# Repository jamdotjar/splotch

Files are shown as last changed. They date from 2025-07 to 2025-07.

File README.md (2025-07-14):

Card_Outline(3)
# SPLOTCH:
(**S**CARA **PLOT**ter that's **CH**eap).

SPLOTCH is a parallel arm SCARA plotter, that can *usually* trick people into
thinking it draws what it's meaning to.

This project was built in 72 hours as part of the Undercity Hackathon in SF, and
it's state does represent that.



https://youtu.be/LqYqyEfOcu8

# Development
Going into this, I had literally no idea how to make a robot arm, and here I am
now, with still almost no idea how to make a robot arm.  Anyways, we made this.
We started by researching different mechanisms, we settled on this because it
didn't need a belt, and kept the arms relatively light. Servos were used for
their relative ease of use over steppers, and the fact they didn't need
dedicated driver boards which were in very short supply.  The first versions of
the arm assembly were designed to not require screws, but the relative
unreliability of PLA lead to a lot of broken parts, and thus the decisiion to
screw literally everything together. ( exept for the pen holder, which was most
efficient to do snap fit )

# Make your own!
Considering the relatively lightweight requirements, you can build your own SCARA plotter with a few servos, some 3d printed parts, and a pen. Specifically, you will need:
| Component | Description | Quantity | Link |
|---|---|---|---|
| Servos | G996R or similar for arm joints, and pen lifter | 3 | https://towerpro.com.tw/product/sg90-analog/ |
| 3D printed parts | 4 3D printed arms, servo holder, and case | 1 | |
| Rotary encoders | For manual control (etch-a-sketch mode!), we used EC11's | 2 | |
| Pen | Any standard pen or marker, should be no more than 9mm in diameter near the head. | 1 | | 
| Microcontroller | Raspberry Pi pico | 1 | https://www.raspberrypi.com/products/raspberry-pi-pico/ |
| Wiring | Dupont Jumper wires| ~ |  |
| Sticky tape or glue | For securing the servos, double sided tape is pretty good | ~ | |
| Breadboard | wiring aid | 1| |
| M.2 screws longer than 5mm | for attaching arms together | 4 |
| Baseplate | A flat-ish base to mount everything on, we used cardboard| 1 | |

### Assembly
1. Print all 3D parts, or get some elsewhere.
2. put the servos in the holder, and fix them in place with double sided tape or
   glue.
3. Attach the holder to the baseplate, in the center of the bottom edge. The
   curved corners of the baseplate should be facing forwards, and the wires of
   the servos should be facing backwards.
4. Attach the front and back links of each arm. The m.2 screw should pass
   through the first arm and bore into the second arm, securing them together
   and allowing room for rotation. The screws on the two front arms will face
   opposite directions, and the screws on the two back arms will face opposite
   directions.
   The front arm should be on the top, and the back arm should be on the bottom.

   

6. Attach the third servo to the end of the arm, in the small slot.
7. Wire up the motors, and rotary encoders, referencing this wiring diagram:


8. attach the breadboard and servo holder to the baseplate
9. Place the case over the breadboard, make sure to reconnect wires properly
10. Insert rotary encoders into the slots on the lid (maybe use glue), slide in
   the lid.
11. Done!

# Usage
1. Connect the Raspberry Pi Pico to your computer via USB.
2. Setup python enviroment by running:
```bash
pip install -r requirements.txt
```
3. Flash the firmware to the Pico by running:
```bash
mpremote connect auto fs cp firmware/main.py :
```
4. use minicom or any other serial terminal to connect to the Pico:
```bash
minicom -D /dev/tty.usbmodem1101 -b 115200
```
5. Once connected, you can send commands to the plotter, you can use the
   following commands:
   - `angle_a,angle_b` - Move to servo angles (e.g. `120,60`)
   - `xy:x,y` - Move to XY coordinates (e.g. `xy:50,80`)
   - `pen:up`, `pen:down` or `pen:dot` - Move pen up or down, or do both
     (down-up)
   - `safe:x,y,w,h` - Set safe zone (paper) parameters (e.g.
     `safe:-50,100,100,100`)
   - `safe:on` or `safe:off` - Enable or disable safe zone checks
   - `enc:on` or `enc:off` - Enable or disable encoder (manual) control")
   - `enc:step:N` - Set encoder sensitivity (N = degrees per step, e.g.
     `enc:step:0.5`
   - `exit` - Quit program
  Command can be chained together with a semicolon, e.g.
  `angle_a,angle_b;xy:x,y;pen:up`
6. To generate complex strings of commands, you can either use visualizeIK.py to
   draw your own, or use the SVG to commands script to convert an SVG file into
   a set of commands.
7. - Use ik_path_planner.py to draw your own commands:
   - Run `python3 firmware/ik_path_planner.py`
   - Click on the canvas to add a point, adding subsequent points will create a
     line between them. To raise the head, click the "Pen Up" button, and to
     lower it, click the "Pen Down" button. to create a dot at your current
     position, click the "Pen Dot" button.
   - Once you are done, click the "Generate Commands" button to generate a set
     of commands based on the points you have drawn.
   - The generated commands will be printed to the console.
   - Copy the commands to your clipboard and paste them into the serial terminal
     to see them executed.



# Images




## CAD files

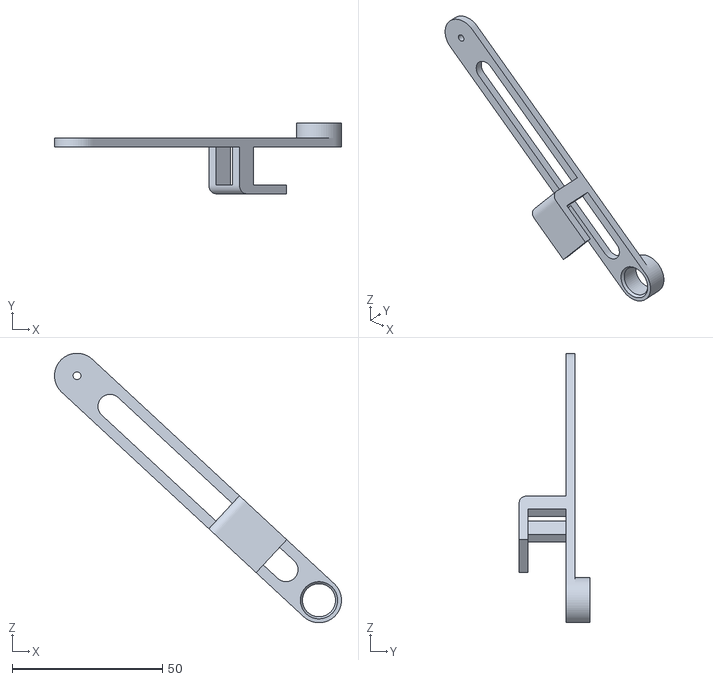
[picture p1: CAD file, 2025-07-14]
CAD/holderarm.stl
95.6 x 23.5 x 89.8

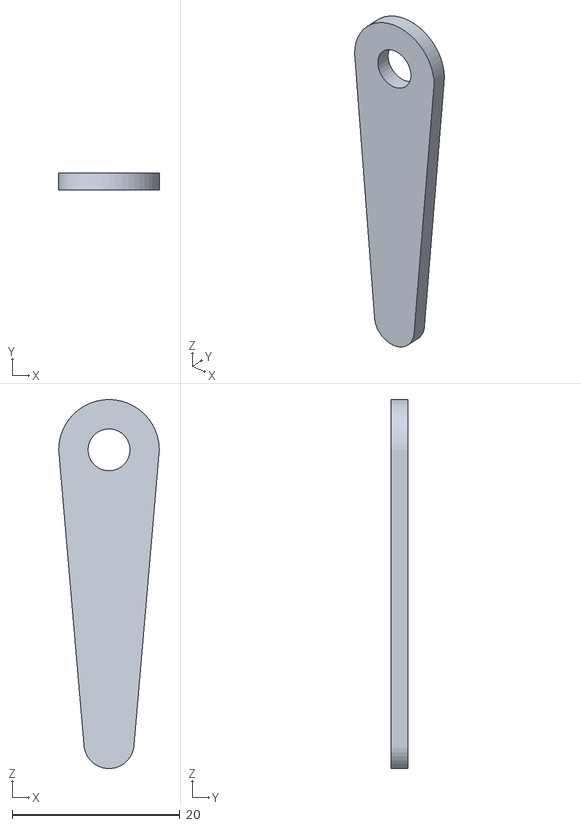
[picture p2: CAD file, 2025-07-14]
CAD/penlift.stl
12.0 x 2.00 x 44.0

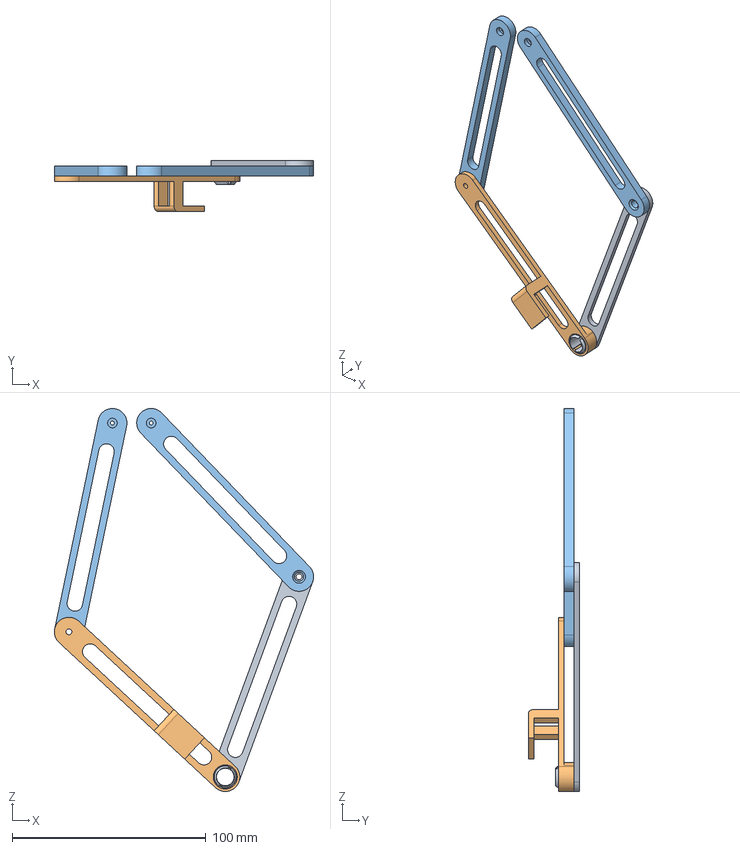
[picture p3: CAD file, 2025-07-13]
CAD/linkage.step
133.7 x 26.5 x 197.5 mm

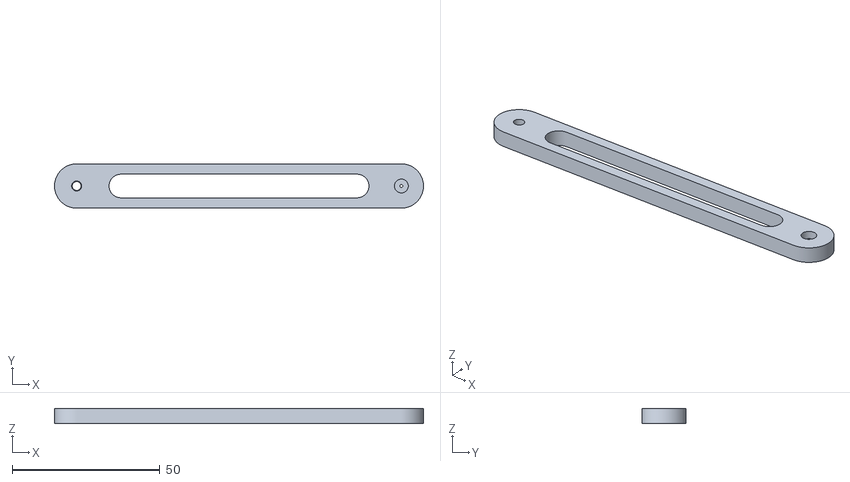
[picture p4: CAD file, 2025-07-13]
CAD/Component3.stl
125.0 x 15.0 x 5.00

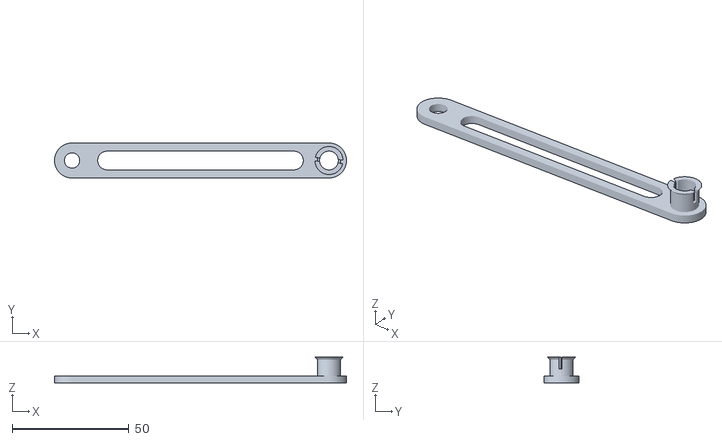
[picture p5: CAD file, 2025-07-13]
CAD/Component1.stl
125.0 x 15.0 x 11.0

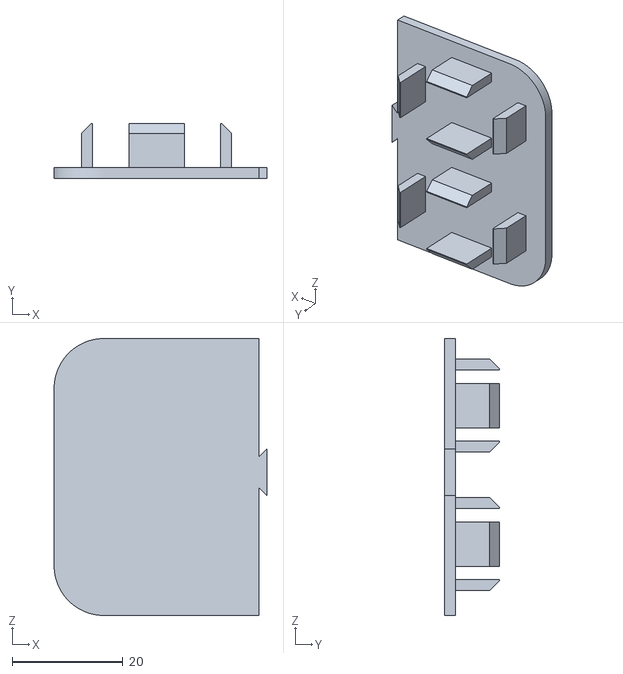
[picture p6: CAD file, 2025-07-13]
CAD/motorholder.stl
38.4 x 10.0 x 50.0

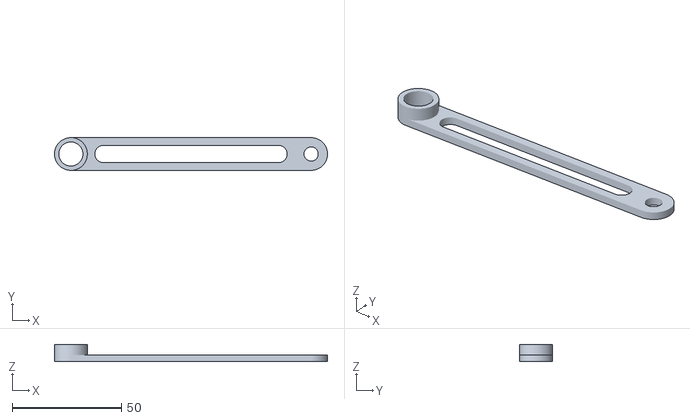
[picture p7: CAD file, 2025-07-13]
CAD/Component2.stl
125.0 x 15.0 x 8.00

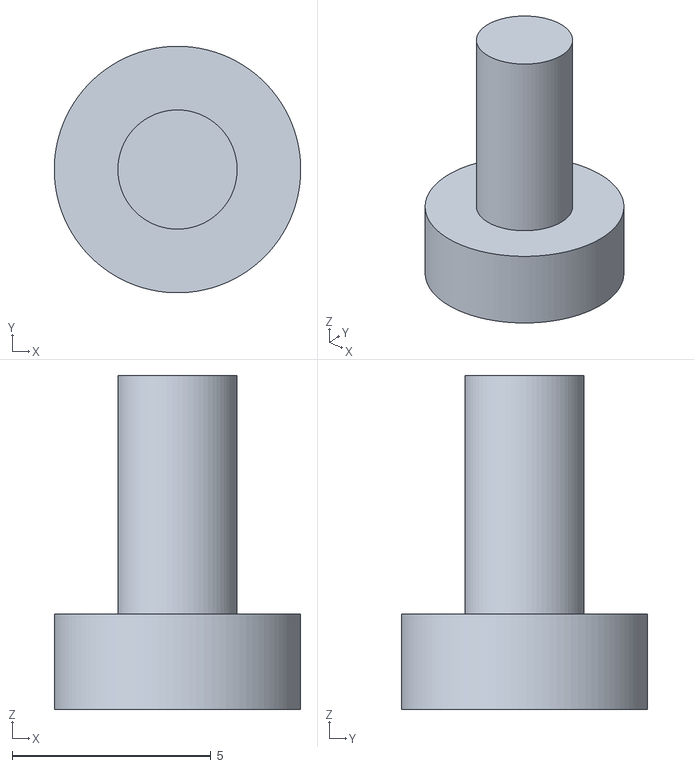
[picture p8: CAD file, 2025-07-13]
CAD/pin.stl
6.20 x 6.20 x 8.40

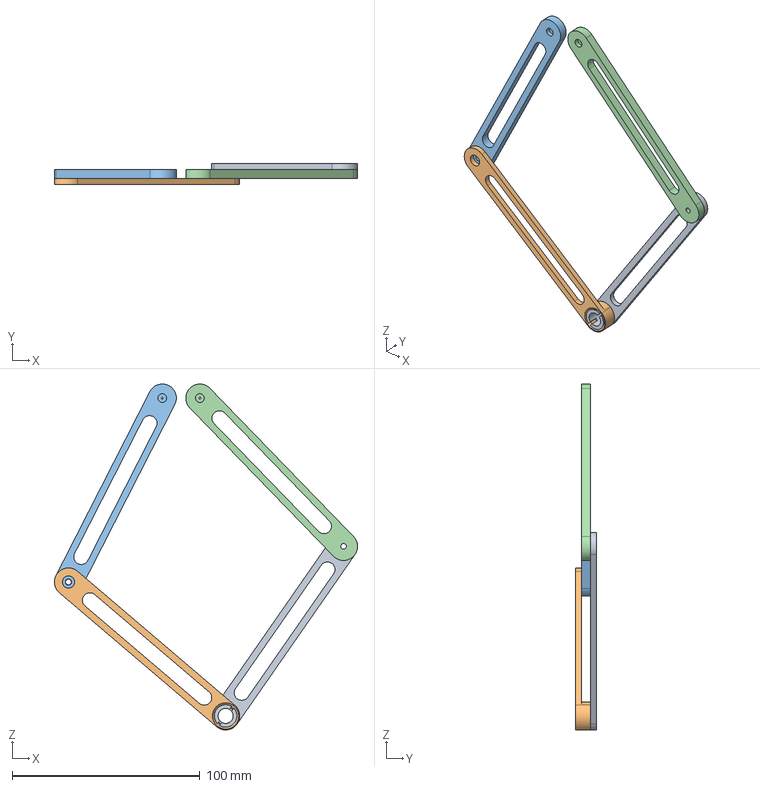
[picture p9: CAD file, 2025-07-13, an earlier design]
CAD/linkage v3.step
161.5 x 11.0 x 184.3 mm

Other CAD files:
CAD/Component4.stl
CAD/linkage.3mf

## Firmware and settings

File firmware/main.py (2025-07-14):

import sys
from servo import Servo
import math
import time
import machine
from machine import Pin

class RotaryEncoder:
    def __init__(self, pin_a, pin_b, callback=None):
        """
        Initialize rotary encoder on the specified pins
        pin_a: CLK pin
        pin_b: DT pin
        callback: Function to call when rotation is detected with direction as parameter (-1 or 1)
        """
        self.pin_a = Pin(pin_a, Pin.IN, Pin.PULL_UP)
        self.pin_b = Pin(pin_b, Pin.IN, Pin.PULL_UP)
        self.last_a = self.pin_a.value()
        self.last_b = self.pin_b.value()
        self.callback = callback
        self.value = 0
        self.last_encoder_time = time.time()
        self.debounce_time = 0.005  # 5ms debounce
        
        # Set up interrupts
        self.pin_a.irq(trigger=Pin.IRQ_FALLING | Pin.IRQ_RISING, handler=self._on_pin_change)
    
    def _on_pin_change(self, pin):
        """Interrupt handler for pin change"""
        current_time = time.time()
        # Debounce
        if current_time - self.last_encoder_time < self.debounce_time:
            return
            
        self.last_encoder_time = current_time
        
        # Read current pin states
        a_val = self.pin_a.value()
        b_val = self.pin_b.value()
        
        # Only process if A pin has changed
        if a_val != self.last_a:
            direction = 0
            
            # Determine direction based on the state of B when A changes
            if a_val == 0:  # Falling edge of A
                direction = -1 if b_val == 0 else 1
            else:  # Rising edge of A
                direction = 1 if b_val == 0 else -1
                
            # Update value
            self.value += direction
                
            # Call the callback if set
            if self.callback and direction != 0:
                self.callback(direction)
                
        # Save current pin states
        self.last_a = a_val
        self.last_b = b_val

class Plotter:
    def __init__(self):
        # pen lift servo angles
        self.penZUp = 30
        self.penZDown = 45

        self.C2 = 12.75  # C/2, where C is the distance between the two servos
        self.totalDist = 56.5  # distance btwn origin and servos midpoint
        self.v = 57.295  # 180/pi

        # SCARA IK parameters
        self.l1 = 110  # first link length
        self.l2 = 110  # second link length
        self.d = 25.5  # distance between arm origins

        # limits
        self.Xmax = 100
        self.Xmin = -100
        self.Ymax = 100
        self.Ymin = -100
        
        # Safe zone parameters (configurable paper area)
        self.safe_zone_enabled = True
        self.safe_zone_width = 100  # mm
        self.safe_zone_height = 100  # mm
        self.safe_zone_x = -50  # mm (left edge position)
        self.safe_zone_y = -200  # mm (bottom edge position)
        
        # Servo angle limits (degrees)
        self.servo_min = 0
        self.servo_max = 180

        # Initialize servos on GPIO pins (change pins as needed)
        self.xservo = Servo(6)
        self.yservo = Servo(7)
        self.penservo = Servo(8)

        self.actuatorPos = {'x': 0.0, 'y': 0.0}
        
        # Track current servo positions for smooth movement
        self.current_a = 90
        self.current_b = 90
        
        # Encoder movement sensitivity
        self.encoder_step = 1.0  # degrees per encoder step
        self.encoder_enabled = False
        
        # Initialize rotary encoders (default pins, can be changed if needed)
        self.encoder_a = None
        self.encoder_b = None
        
        # Set default movement speed
        self.setMovementSpeed('normal')

        self.penUp()
        self.xservo.move(90)
        self.yservo.move(90)
        time.sleep(0.5)

    def penUp(self):
        self.penservo.move(self.penZUp)
        time.sleep(0.5)

    def penDown(self):
        self.penservo.move(self.penZDown)
        time.sleep(0.5)

    def servowrite(self, a, b, smooth=True):
        """
        Move servos to target angles with optional smooth movement
        """
        target_a = round(a)
        target_b = round(b)
        
        # Update current positions first
        if not hasattr(self, 'current_a'):
            self.current_a = 90
        if not hasattr(self, 'current_b'):
            self.current_b = 90
            
        current_a = self.current_a
        current_b = self.current_b
        
        if not smooth:
            # Direct movement (fast)
            self.xservo.move(target_a)
            self.yservo.move(target_b)
            self.current_a = target_a
            self.current_b = target_b
            time.sleep(0.05)
            return
        
        # Calculate movement distance
        diff_a = abs(target_a - current_a)
        diff_b = abs(target_b - current_b)
        max_diff = max(diff_a, diff_b)
        
        # For any movement, just move directly but with appropriate delay
        self.xservo.move(target_a)
        self.yservo.move(target_b)
        self.current_a = target_a
        self.current_b = target_b
        
        # Scale delay based on movement distance
        movement_delay = max(0.1, max_diff * 0.008)  # 8ms per degree of movement
        time.sleep(movement_delay)

    def setMovementSpeed(self, speed='normal'):
        """
        Set movement speed for servo operations
        speed: 'slow', 'normal', 'fast'
        """
        if speed == 'slow':
            self.servo_delay = 0.1
            self.servo_steps_per_degree = 3
        elif speed == 'fast':
            self.servo_delay = 0.02
            self.servo_steps_per_degree = 0.5
        else:  # normal
            self.servo_delay = 0.05
            self.servo_steps_per_degree = 1.5
    def calcIK(self, x1, y1):
        x = x1
        y = y1
        a1 = self.l1  # first link length
        a2 = self.l2  # second link length
        d = self.d  # distance between arm origins

        try:
            # Calculate distances
            c = math.sqrt((x**2) + (y**2))  # distance from left arm origin to target
            e = math.sqrt(((d-x)**2) + (y**2))  # distance from right arm origin to target
            
            # Check if target is within reach for both arms
            if c > a1 + a2 or c < abs(a1 - a2):
                print(f"Position ({x}, {y}) is out of reach for left arm")
                return None, None
            if e > a1 + a2 or e < abs(a1 - a2):
                print(f"Position ({x}, {y}) is out of reach for right arm")
                return None, None
                
            # Calculate elbow angles
            cos_q2_left = (c**2 - a1**2 - a2**2) / (2 * a1 * a2)
            if abs(cos_q2_left) > 1:
                print(f"Left arm: Invalid cosine value {cos_q2_left}")
                return None, None
            q2_left = math.acos(cos_q2_left)
            
            cos_q2_right = (e**2 - a1**2 - a2**2) / (2 * a1 * a2)
            if abs(cos_q2_right) > 1:
                print(f"Right arm: Invalid cosine value {cos_q2_right}")
                return None, None
            q2_right = -math.acos(cos_q2_right)
            
            # Calculate shoulder angles
            if x == 0:
                q1_left = math.pi/2 if y > 0 else -math.pi/2
            else:
                k1 = a1 + a2 * math.cos(q2_left)
                k2 = a2 * math.sin(q2_left)
                q1_left = math.atan2(y, x) - math.atan2(k2, k1)
                
            x_right = x - d
            if x_right == 0:
                q1_right = math.pi/2 if y > 0 else -math.pi/2
            else:
                k1_right = a1 + a2 * math.cos(q2_right)
                k2_right = a2 * math.sin(q2_right)
                q1_right = math.atan2(y, x_right) - math.atan2(k2_right, k1_right)
            
            # Convert to degrees for servo control
            alpha_deg = math.degrees(q1_left)
            beta_deg = math.degrees(q1_right)
            
            # IMPORTANT: For display purposes, we want to use the mirrored angles
            # similar to what's shown in the visualizer
            display_y = -y if y > 0 else y
            display_alpha, display_beta = self.calcDisplayAngles(x, display_y)
            
            # Return display angles for actual servo control
            return -display_alpha, -display_beta
            
        except (ValueError, ZeroDivisionError) as e:
            print(f"Error calculating IK for ({x}, {y}): {e}")
            return None, None
            
    def calcDisplayAngles(self, x, y):
        """
        Helper function to calculate display angles (mirrored angles)
        These are the angles shown in the visualizer
        """
        a1 = self.l1
        a2 = self.l2
        d = self.d
        
        try:
            c = math.sqrt((x**2) + (y**2))
            e = math.sqrt(((d-x)**2) + (y**2))
            
            if c > a1 + a2 or c < abs(a1 - a2) or e > a1 + a2 or e < abs(a1 - a2):
                return None, None
                
            cos_q2_left = (c**2 - a1**2 - a2**2) / (2 * a1 * a2)
            if abs(cos_q2_left) > 1:
                return None, None
            q2_left = math.acos(cos_q2_left)
            
            if x == 0:
                q1_left = math.pi/2 if y > 0 else -math.pi/2
            else:
                k1 = a1 + a2 * math.cos(q2_left)
                k2 = a2 * math.sin(q2_left)
                q1_left = math.atan2(y, x) - math.atan2(k2, k1)
                
            x_right = x - d
            cos_q2_right = (e**2 - a1**2 - a2**2) / (2 * a1 * a2)
            if abs(cos_q2_right) > 1:
                return None, None
            q2_right = -math.acos(cos_q2_right)
            
            if x_right == 0:
                q1_right = math.pi/2 if y > 0 else -math.pi/2
            else:
                k1_right = a1 + a2 * math.cos(q2_right)
                k2_right = a2 * math.sin(q2_right)
                q1_right = math.atan2(y, x_right) - math.atan2(k2_right, k1_right)
                
            return math.degrees(q1_left), math.degrees(q1_right)
            
        except (ValueError, ZeroDivisionError):
            return None, None

    def drawLine(self, x1, y1):
        """
        Move to target position using SCARA inverse kinematics
        """
        # Clamp coordinates
        x1 = max(min(x1, self.Xmax), self.Xmin)
        y1 = max(min(y1, self.Ymax), self.Ymin)
        
        # Check if the point is within the safe zone (paper area)
        in_safe_zone = self.is_point_in_safe_zone(x1, y1)
        if not in_safe_zone and self.safe_zone_enabled:
            print(f"WARNING: Position ({x1}, {y1}) is outside the safe zone (paper area)")
            # Continue anyway, but give a warning

        # Calculate servo angles using IK
        alpha, beta = self.calcIK(x1, y1)
        
        if alpha is not None and beta is not None:
            # Update current position
            self.actuatorPos['x'] = x1
            self.actuatorPos['y'] = y1
            
            # Move servos to calculated angles
            self.servowrite(alpha, beta)
            print(f"Moving to ({x1}, {y1}) -> Servo angles: α={alpha:.1f}°, β={beta:.1f}°")
            if not in_safe_zone and self.safe_zone_enabled:
                print("CAUTION: Point is outside the paper area!")
        else:
            print(f"Cannot reach position ({x1}, {y1})")

    def testIK(self):
        """
        Test the IK implementation with known values
        """
        print("Testing IK implementation...")
        
        # Test with the example values from the provided code
        test_x, test_y = 1, 7
        alpha, beta = self.calcIK(test_x, test_y)
        
        if alpha is not None and beta is not None:
            print(f"Test position ({test_x}, {test_y}):")
            print(f"Left arm angle (α): {alpha:.2f}°")
            print(f"Right arm angle (β): {beta:.2f}°")
            
            # Verify against the expected results from your code
            # Expected: t1 ≈ 55.77°, t2 ≈ 127.38°
            print(f"Expected results: α ≈ 55.77°, β ≈ 127.38°")
        else:
            print(f"Failed to calculate IK for test position ({test_x}, {test_y})")
        
        print("IK test complete.\n")
    
    def is_point_in_safe_zone(self, x, y):
        """
        Check if a point is within the safe zone (paper area)
        Returns True if the point is within the safe zone, False otherwise
        """
        return (self.safe_zone_enabled and
                self.safe_zone_x <= x <= self.safe_zone_x + self.safe_zone_width and
                self.safe_zone_y - self.safe_zone_height <= y <= self.safe_zone_y)
                
    def init_encoders(self, pin_a1, pin_b1, pin_a2, pin_b2):
        """
        Initialize the rotary encoders for manual arm control
        pin_a1, pin_b1: pins for first encoder (controls first servo)
        pin_a2, pin_b2: pins for second encoder (controls second servo)
        """
        # Initialize encoders with callbacks
        self.encoder_a = RotaryEncoder(pin_a1, pin_b1, self.on_encoder_a_change)
        self.encoder_b = RotaryEncoder(pin_a2, pin_b2, self.on_encoder_b_change)
        self.encoder_enabled = True
        print("Rotary encoders initialized. Manual arm control enabled.")
        
    def on_encoder_a_change(self, direction):
        """
        Handle changes in the first encoder (controlling the first arm)
        direction: 1 for clockwise, -1 for counter-clockwise
        """
        if not self.encoder_enabled:
            return
            
        # Update the angle based on direction and step size
        new_angle = self.current_a + (direction * self.encoder_step)
        
        # Clamp to valid range
        new_angle = max(min(new_angle, self.servo_max), self.servo_min)
        
        # Move the servo
        if new_angle != self.current_a:
            self.xservo.move(new_angle)
            self.current_a = new_angle
            print(f"Encoder A: Servo A moved to {new_angle:.1f}°")
        
    def on_encoder_b_change(self, direction):
        """
        Handle changes in the second encoder (controlling the second arm)
        direction: 1 for clockwise, -1 for counter-clockwise
        """
        if not self.encoder_enabled:
            return
            
        # Update the angle based on direction and step size
        new_angle = self.current_b + (direction * self.encoder_step)
        
        # Clamp to valid range
        new_angle = max(min(new_angle, self.servo_max), self.servo_min)
        
        # Move the servo
        if new_angle != self.current_b:
            self.yservo.move(new_angle)
            self.current_b = new_angle
            print(f"Encoder B: Servo B moved to {new_angle:.1f}°")
    
    def set_encoder_enabled(self, enabled):
        """
        Enable or disable the rotary encoders
        enabled: True to enable, False to disable
        """
        self.encoder_enabled = enabled
        status = "enabled" if enabled else "disabled"
        print(f"Rotary encoder control {status}")
        
    def set_encoder_sensitivity(self, step):
        """
        Set the sensitivity of the rotary encoders
        step: degrees to move per encoder step
        """
        self.encoder_step = float(step)
        print(f"Encoder sensitivity set to {step} degrees per step")
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

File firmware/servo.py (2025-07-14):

"""Basic servo library."""
import machine
import math

class Servo:
    def __init__(self,pin_id,min_us=544.0,max_us=2400.0,min_deg=0.0,max_deg=180.0,freq=50):
        self.pwm = machine.PWM(machine.Pin(pin_id))
        self.pwm.freq(freq)
        self.current_us = 0.0
        self._slope = (min_us-max_us)/(math.radians(min_deg)-math.radians(max_deg))
        self._offset = min_us

    def move(self, deg):
        self.write(deg)

    def write(self,deg):
        self.write_rad(math.radians(deg))

    def read(self):
        return math.degrees(self.read_rad())

    def write_rad(self,rad):
        self.write_us(rad*self._slope+self._offset)

    def read_rad(self):
        return (self.current_us-self._offset)/self._slope

    def write_us(self,us):
        self.current_us=us
        self.pwm.duty_ns(int(self.current_us*1000.0))

    def read_us(self):
        return self.current_us

    def off(self):
        self.pwm.duty_ns(0)

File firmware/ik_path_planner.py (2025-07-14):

import matplotlib.pyplot as plt
import matplotlib.patches as patches
import matplotlib.widgets as widgets
import math
import numpy as np
import signal
import atexit

# For copying to clipboard - try to import but provide fallback
try:
    import pyperclip
    HAS_PYPERCLIP = True
except ImportError:
    HAS_PYPERCLIP = False
    print("pyperclip not available, will print commands to console instead.")
    print("To install: pip install pyperclip")

# Track application state for clean exit
app_running = True

def signal_handler(sig, frame):
    """Handle termination signals gracefully"""
    global app_running
    print("\nReceived termination signal. Cleaning up...")
    app_running = False
    plt.close('all')
    
# Register signal handlers
signal.signal(signal.SIGINT, signal_handler)
signal.signal(signal.SIGTERM, signal_handler)

class IKPathPlanner:
    def __init__(self):
        # Same parameters as your Plotter class
        self.l1 = 110  # first link length
        self.l2 = 110  # second link length
        self.d = 25.5  # distance between arm origins
        
        # Safe zone parameters (configurable paper area)
        self.safe_zone_enabled = True
        self.safe_zone_width = 100  # mm
        self.safe_zone_height = 100  # mm
        self.safe_zone_x = -50+self.d/2  # mm (left edge position)
        self.safe_zone_y = -100  # mm (bottom edge position)
        
        # Keep track of current position and pen state
        self.current_x = 0
        self.current_y = 0
        self.pen_down = False
        
        # Command sequence
        self.commands = []
        self.path_points = []  # [(x, y, pen_state, alpha, beta), ...]
        self.current_command_id = 0
        
        # Set up the plot with fixed size and axes limits
        self.fig = plt.figure(figsize=(12, 10))
        
        # Create a grid layout for our plot and controls
        self.gs = self.fig.add_gridspec(3, 2, height_ratios=[4, 1, 1], width_ratios=[4, 1])
        
        # Main plot area
        self.ax = self.fig.add_subplot(self.gs[0, :])
        self.ax.set_xlim(-150, 150)
        self.ax.set_ylim(-200, 50)
        self.ax.set_aspect('equal')
        self.ax.grid(True, alpha=0.3)
        self.ax.set_title('SCARA Plotter Path Planner with IK')
        
        # Controls area
        self.controls_ax = self.fig.add_subplot(self.gs[1, 0])
        self.controls_ax.set_axis_off()
        
        # Status area
        self.status_ax = self.fig.add_subplot(self.gs[1, 1])
        self.status_ax.set_axis_off()
        
        # Commands list area
        self.command_list_ax = self.fig.add_subplot(self.gs[2, :])
        self.command_list_ax.set_axis_off()
        
        # Arm origins
        self.left_origin = np.array([0, 0])
        self.right_origin = np.array([self.d, 0])
        
        # Add control buttons
        self.setup_buttons()
        
        # Display initial command list
        self.update_command_list()
    
    def setup_buttons(self):
        """Set up UI control buttons"""
        # Use the controls axis for button placement
        self.controls_ax.set_position([0.1, 0.05, 0.8, 0.1])  # [left, bottom, width, height]
        
        # Position buttons within the controls axis
        button_width = 0.15
        button_height = 0.6
        button_spacing = 0.02
        start_x = 0.02
        start_y = 0.2
        
        # Pen up button
        pen_up_pos = [start_x, start_y, button_width, button_height]
        self.btn_pen_up = widgets.Button(
            self.controls_ax.inset_axes(pen_up_pos),
            'Pen Up',
            color='lightgreen',
            hovercolor='lime'
        )
        self.btn_pen_up.on_clicked(self.on_pen_up)
        
        # Pen down button
        pen_down_pos = [start_x + (button_width + button_spacing), start_y, button_width, button_height]
        self.btn_pen_down = widgets.Button(
            self.controls_ax.inset_axes(pen_down_pos),
            'Pen Down',
            color='salmon',
            hovercolor='tomato'
        )
        self.btn_pen_down.on_clicked(self.on_pen_down)
        
        # Add dot button
        dot_pos = [start_x + 2 * (button_width + button_spacing), start_y, button_width, button_height]
        self.btn_dot = widgets.Button(
            self.controls_ax.inset_axes(dot_pos),
            'Add Dot',
            color='skyblue',
            hovercolor='deepskyblue'
        )
        self.btn_dot.on_clicked(self.on_add_dot)
        
        # Toggle safe zone button
        toggle_pos = [start_x + 3 * (button_width + button_spacing), start_y, button_width, button_height]
        self.btn_toggle_safe = widgets.Button(
            self.controls_ax.inset_axes(toggle_pos),
            'Toggle Safe Zone',
            color='lightgray',
            hovercolor='darkgray'
        )
        self.btn_toggle_safe.on_clicked(self.on_toggle_safe)
        
        # Clear path button
        clear_pos = [start_x + 4 * (button_width + button_spacing), start_y, button_width, button_height]
        self.btn_clear = widgets.Button(
            self.controls_ax.inset_axes(clear_pos),
            'Clear Path',
            color='pink',
            hovercolor='hotpink'
        )
        self.btn_clear.on_clicked(self.on_clear_path)
        
        # Copy commands button
        copy_pos = [start_x + 5 * (button_width + button_spacing), start_y, button_width, button_height]
        self.btn_copy = widgets.Button(
            self.controls_ax.inset_axes(copy_pos),
            'Copy Commands',
            color='lightyellow',
            hovercolor='yellow'
        )
        self.btn_copy.on_clicked(self.on_copy_commands)
    
    def on_pen_up(self, event):
        """Add pen up command to the queue"""
        self.pen_down = False
        self.add_command("pen:up", None)
        self.update_status("Added: Pen UP command")
        self.draw_path()
    
    def on_pen_down(self, event):
        """Add pen down command to the queue"""
        self.pen_down = True
        self.add_command("pen:down", None)
        self.update_status("Added: Pen DOWN command")
        self.draw_path()
    
    def on_add_dot(self, event):
        """Add a dot command (pen down then up at current location)"""
        # Add commands for the dot (down and up at the current point)
        if len(self.path_points) > 0:
            last_x, last_y, _, last_alpha, last_beta = self.path_points[-1]
            self.add_command("pen:dot", None)
            self.update_status(f"Added: Dot at ({last_x:.1f}, {last_y:.1f}) -> angles [{last_beta:.1f}°, {last_alpha:.1f}°]")
            self.draw_path()
        else:
            self.update_status("Can't add dot: No position set")
    
    def on_toggle_safe(self, event):
        """Toggle the safe zone visibility"""
        self.safe_zone_enabled = not self.safe_zone_enabled
        status = "visible" if self.safe_zone_enabled else "hidden"
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

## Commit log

2025-07-13 3d models
    [Component1.stl, Component2.stl, Component3.stl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]
2025-07-13 demo state
    [linkage.step]
2025-07-13 started adding pen servo code
2025-07-14 both servos work
2025-07-14 Visualized the new IK system
    [penlift.stl]
2025-07-14 works with minicom
    [holderarm.stl]
2025-07-14 multiple commands at once
    [holderarm.stl, penlift.stl]
2025-07-14 add rotary encoders
